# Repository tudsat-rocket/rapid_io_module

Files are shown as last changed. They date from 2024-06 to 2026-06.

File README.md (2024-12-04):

# I/O module

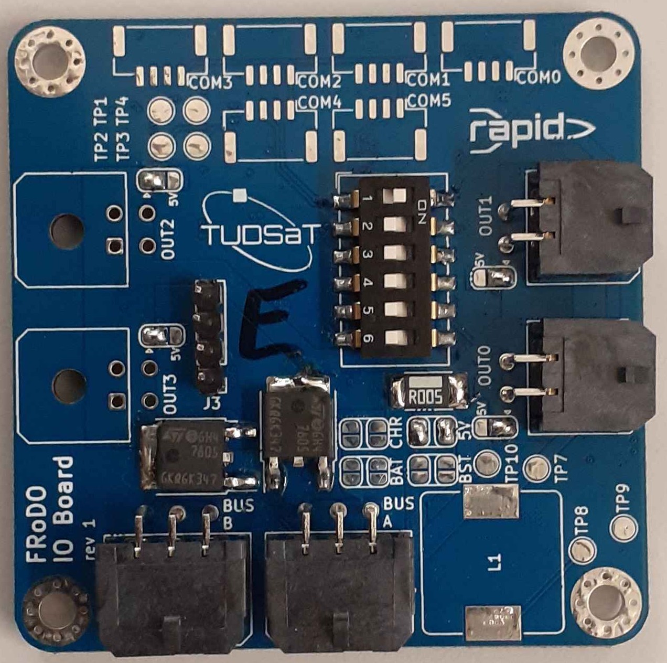
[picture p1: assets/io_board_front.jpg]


The I/O module is built as a general board for various sensor inputs and outputs. It is run by an STM32F103.

The module features 4 output connectors, with each being usable both as a servo output or 2 switchable outputs, powered by one of a variety of power sources. They also feature a variety of communication ports, allowing the connection to UART, I2C systems as well as the use of the STM32's ADC.

The outputs of the I/O module can be powered straight from the FC battery, a 5v line powered by a linear regulator, an external source like the charge bus or an auxiliary battery, or an onboard, programmable boost converter.

## Components

- STM32F103
- 4x output connector
- 2x switchable outputs
- see schematics for complete list

## Firmware

The firmware for the IO-board is written in rust, uses [embassy](https://github.com/embassy-rs/embassy) and can be found in the `frimware` folder. 

## Getting started

- clone the repository

- install STLink drivers
  
  - **Linux**: Install via package manager if possible, e.g. `pacman -S stlink`
  
  - **Windows**:
    
    - Download drivers from [ST's website](https://www.st.com/en/development-tools/stsw-link009.html) (requires account)
    - Extract .zip and run `dpinst_amd64.exe` for 64-bit systems, and `dpinst_x86.exe` on 32-bit systems.
    
    After installation, it *may* be necessary to unplug the STLink and plug it back in, or even reboot (or reload udev rules on Linux).

- install **Rustup**
  
  - A tool used to manage different Rust versions and targets (e.g. x86, ARM,
     etc.). Download and run installer: follow the instructions on [https://rustup.rs/](https://rustup.rs/) (Use rustup-init.exe for Windows, defaults are fine)

- **Rust**
  
  - Using `rustup`, we can download the target needed for the STM32 and some other tools we need.
    
    - `rustup target add thumbv7em-none-eabi` (Add ARM toolchain)
    
    - `cargo install probe-rs-tools --locked`
    
    - `cargo install flip-link` (Needed for cargo run)

- **Compiling & Flashing**
  
  - run `cargo run --release`

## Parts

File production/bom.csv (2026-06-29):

Designator | Footprint | Quantity | Value | LCSC Part #
C1 | 0402 | 1 | 4u7
C10, C7 | 0402 | 2 | 10n
C11, C12, C13 | 0805 | 3 | 10u | C440198
C14 | CP_Elec_6.3x4.5 | 1 | 220u | C5379968
C15, C16 | 0805 | 2 | 22u | C45783
C17 | 0805 | 1 | 10u | C15850
C18, C20, C30 | 0402 | 3 | 100n | C1525
C19 | 0603 | 1 | 470n | C1623
C2, C29, C3, C31, C32, C33, C34, C35, C38, C4, C41, C5, C6 | 0402 | 13 | 100n
C21, C22, C23, C24, C36, C37, C39, C40, C42, C43 | 0402 | 10 | 10n | C15195
C25, C26 | 0402 | 2 | 10p
C27 | 0402 | 1 | 10u | C15525
C28 | 0603 | 1 | 22u | C59461
C8, C9 | 0402 | 2 | 1u
D1, D7 | D_SMA | 2 | 700mV@5A | C5140024
D10, D13, D14, D9 | D_SOD-123FL | 4 | D | C64898
D11, D12, D15, D16, D2, D3, D4, D5, D6 | 0603 | 9 | red | C2286
D8 | D_SOD-123 | 1 | ~ | C8598
F1 | 1206 | 1 | 3A | C14165
F2, F3 | 1206 | 2 | 5A | C57525
FB1 | 0603 | 1 | 120R
J15 | USB_C_Receptacle_Palconn_UTC16-G | 1 | USB_C_Receptacle_USB2.0 | C709357
Q1, Q2, Q5, Q6 | SOIC-8_3.9x4.9mm_P1.27mm | 4 | AOSP21321 | C560863
Q10, Q11, Q12, Q9 | SOT-23 | 4 | AO3400A | C20917
R1 | 0402 | 1 | 17k4 | C2933077
R10, R18, R19, R9 | 0603 | 4 | 4k7 | C23162
R11, R38, R39, R7, R8 | 0402 | 5 | 22R | C25092
R12, R13, R15, R16, R20, R21, R23, R24 | 0402 | 8 | 100
R14, R17, R22, R25, R26, R27, R28, R29, R3, R30, R5, R69, R70, R71, R72, R73, R74 | 0402 | 17 | 1k | C11702
R2, R32, R33 | 1206 | 3 | 15m | C601098
R31, R6 | 0402 | 2 | 100k | C25741
R34, R35, R36, R37, R44 | 0402 | 5 | 5k1 | C25905
R4 | 0402 | 1 | 3k3 | C25890
R41, R42, R43 | 0402 | 3 | 15k | C25756
R45, R46, R47 | 0402 | 3 | 2k2 | C25879
R49, R50, R51, R52, R53, R54, R57, R58, R59, R60, R61, R62, R63, R64, R67, R68 | 0402 | 16 | 12k | C25752
R55, R56, R65, R66 | 0402 | 4 | 330 | C25104
SW1, SW2, SW3 | SW_SPST_TS-1088-xR020 | 3 | KMR721NGLFS | C720477
TH1 | 0603 | 1 | 10k
TP1, TP2, TP3, TP4, TP5 | TestPoint_Pad_D1.0mm | 5 | TestPoint
U2 | LQFP-64_10x10mm_P0.5mm | 1 | STM32F105RCTx
U3 | SOT-223-3_TabPin2 | 1 | AZ1117-3.3 | C92102
U4 | SOIC-8_5.3x5.3mm_P1.27mm | 1 | W25Q128JVP
U5, U6 | SOIC-8_3.9x4.9mm_P1.27mm | 2 | MCP2562-E-SN
U7, U8, U9 | SOT-23-6 | 3 | INA181A1 | C45351496
Y1 | Crystal_SMD_5032-4Pin_5.0x3.2mm | 1 | 8MHz 12pF | C2149245

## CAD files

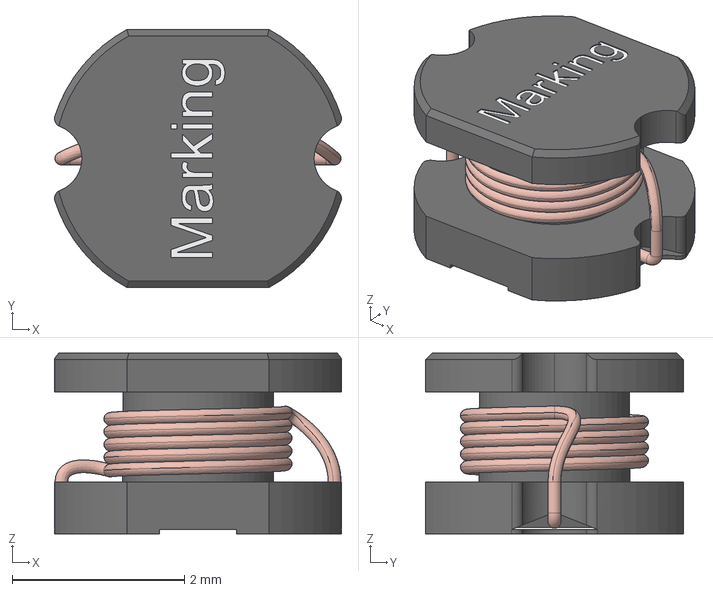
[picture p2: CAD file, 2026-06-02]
3dmodels/L_Wurth_WE-PD2-3521.step
3.34 x 3.00 x 2.10 mm

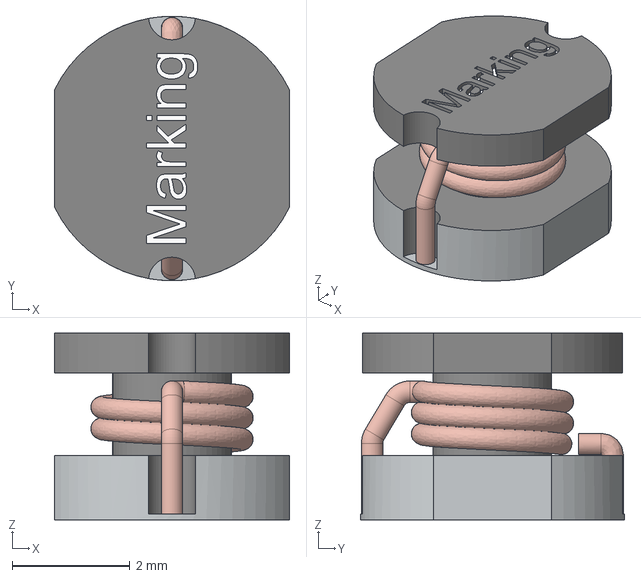
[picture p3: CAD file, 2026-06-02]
3dmodels/L_Wurth_WE-PD2-4532.step
4.00 x 4.50 x 3.18 mm

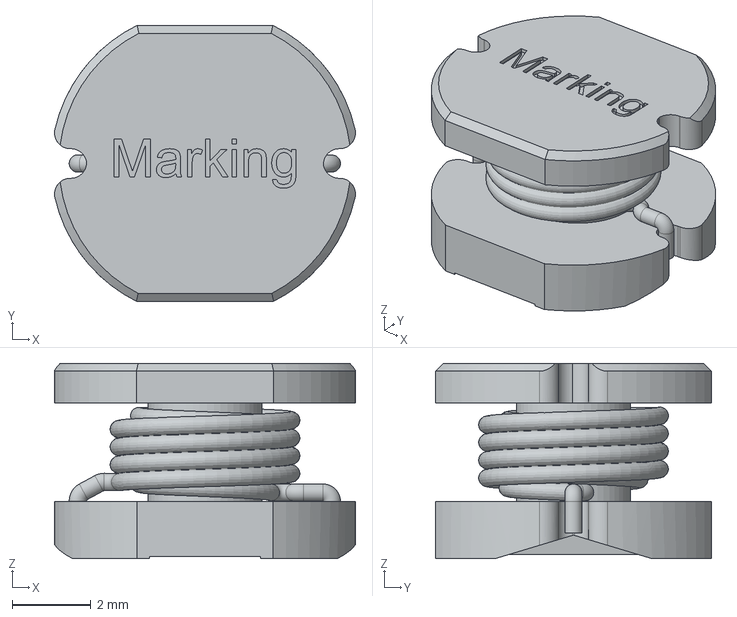
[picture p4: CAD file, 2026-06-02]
3dmodels/L_Wurth_WE-PD2-7850.step
7.63 x 7.00 x 4.95 mm

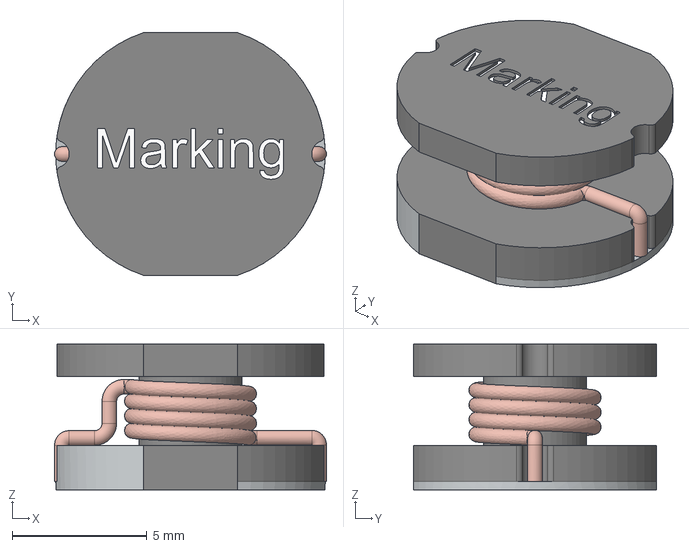
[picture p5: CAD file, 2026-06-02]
3dmodels/L_Wurth_WE-PD2-1054.step
10.1 x 9.00 x 5.40 mm

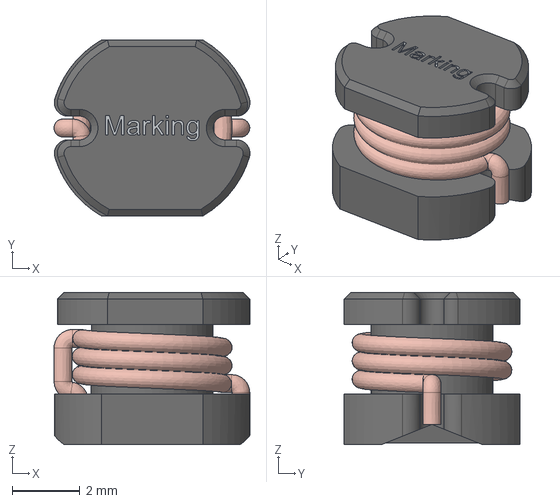
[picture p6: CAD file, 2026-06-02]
3dmodels/L_Wurth_WE-PD2-5848.step
5.79 x 5.20 x 4.50 mm

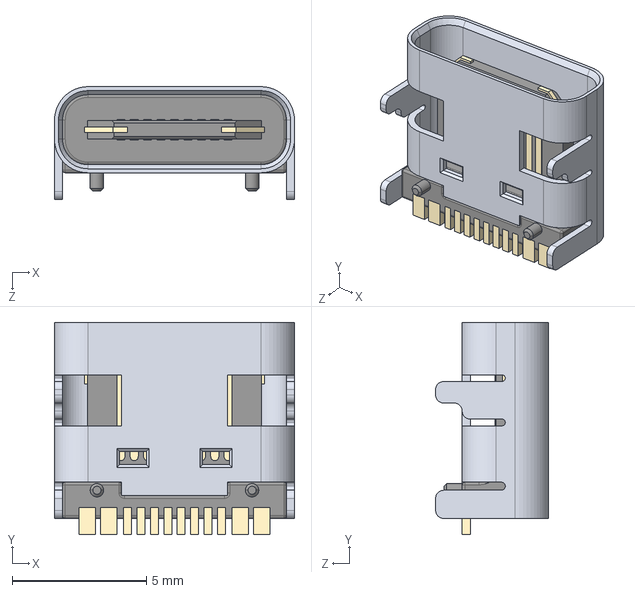
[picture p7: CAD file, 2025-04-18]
3dmodels/usb_c.step
8.94 x 7.90 x 4.20 mm

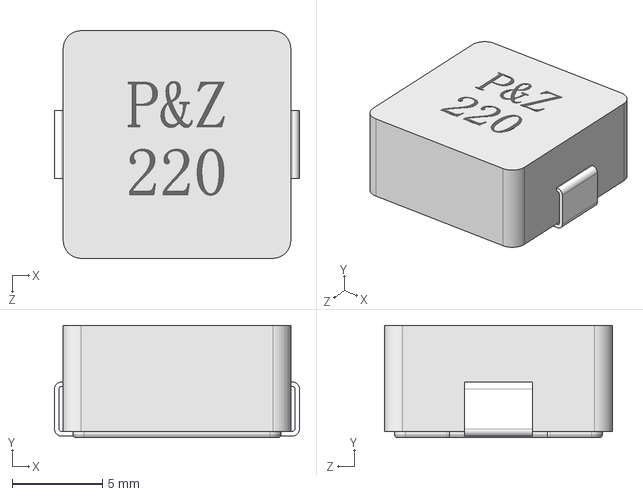
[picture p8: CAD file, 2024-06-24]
3dmodels/PSM1365 Series SMD Molding inductor.STEP
13.6 x 6.21 x 12.6 mm

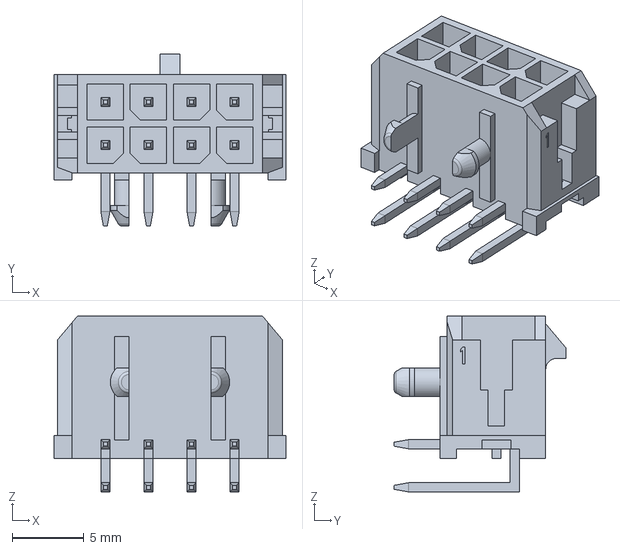
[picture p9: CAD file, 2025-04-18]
3dmodels/430450800.stp
16.1 x 11.9 x 12.2 mm

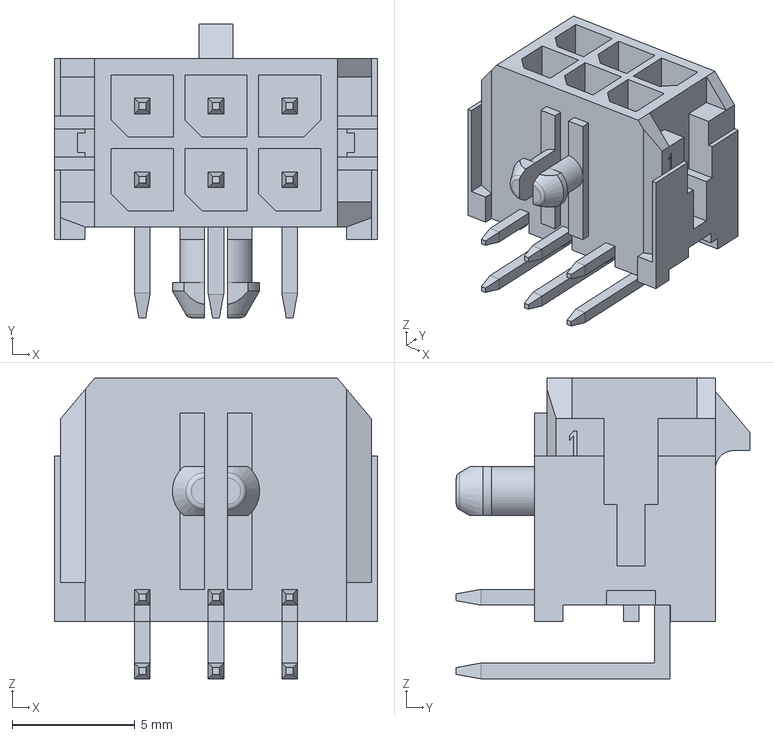
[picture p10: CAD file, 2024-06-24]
3dmodels/430450600.stp
13.2 x 11.9 x 12.2 mm

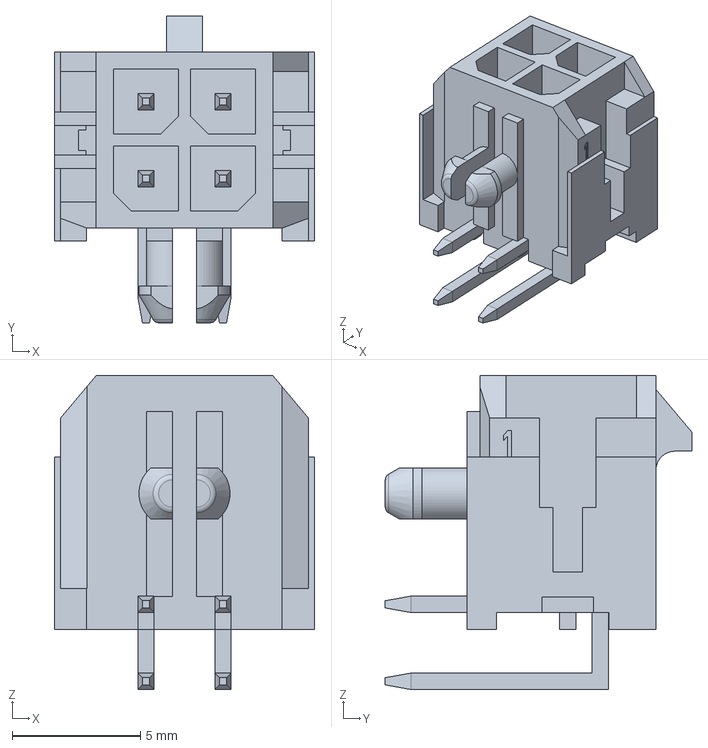
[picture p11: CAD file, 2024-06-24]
3dmodels/430450400.step
10.2 x 11.9 x 12.2 mm

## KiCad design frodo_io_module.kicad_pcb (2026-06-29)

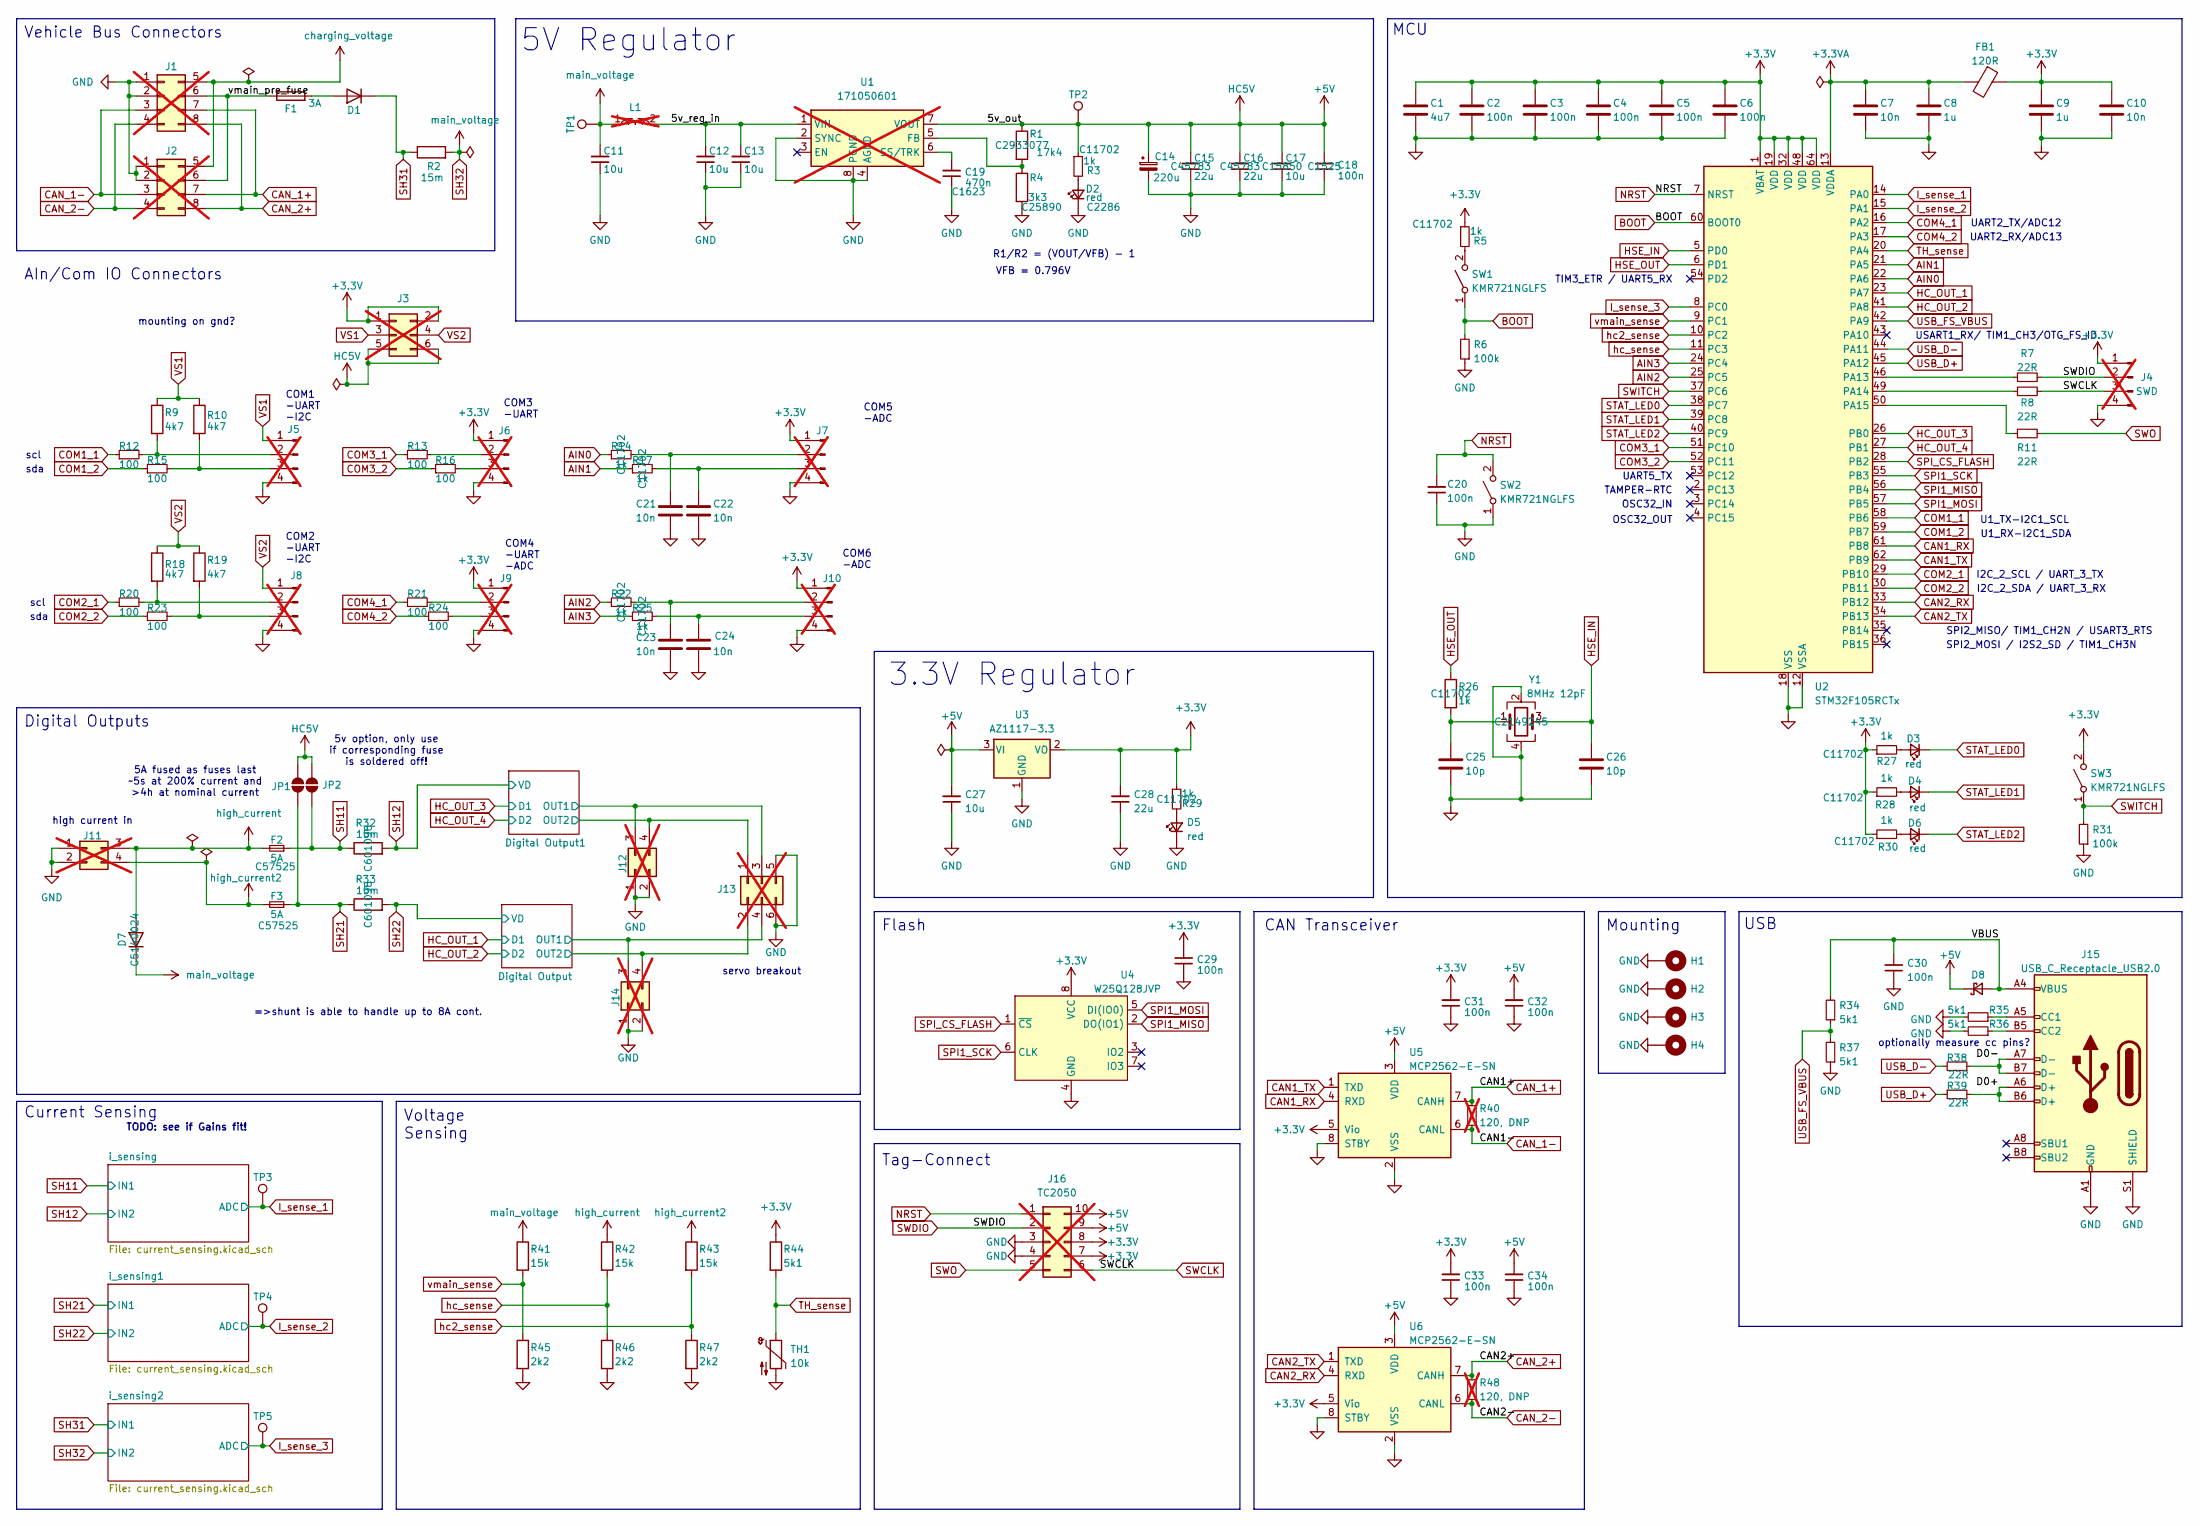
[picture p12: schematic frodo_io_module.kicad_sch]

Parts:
C1: 4u7; C_0402_1005Metric; LCSC# C23733
C2, C3, C4, C5, C6, C29, C31, C32, C33, C34: 100n; C_0402_1005Metric; LCSC# C1525
C7, C10: 10n; C_0402_1005Metric; LCSC# C15195
C8, C9: 1u; C_0402_1005Metric; LCSC# C52923
C11, C12, C13: 10u; C_0805_2012Metric; LCSC C440198
C14: 220u; CP_Elec_6.3x4.5; LCSC C5379968
C15, C16: 22u; C_0805_2012Metric; LCSC C45783
C17: 10u; C_0805_2012Metric; LCSC C15850
C18: 100n; C_0402_1005Metric; LCSC C1525
C19: 470n; C_0603_1608Metric; LCSC C1623
C20, C30: 100n; C_0402_1005Metric; Part# CL10B104KB8NNNC; LCSC C1525
C21, C22, C23, C24: 10n; C_0402_1005Metric; LCSC C15195
C25, C26: 10p; C_0402_1005Metric; LCSC# C32949
C27: 10u; C_0402_1005Metric; Part# CL31B106KAHNNNE; LCSC C15525
C28: 22u; C_0603_1608Metric; Part# GRM155R60J226ME11D; LCSC C59461
D1, D7: 700mV@5A; D_SMA; LCSC C5140024
D2: red; LED_0603_1608Metric; Part# XL-1608SURC-06; LCSC C2286
D3, D4, D5, D6: red; LED_0603_1608Metric; LCSC C2286
D8: D_SOD-123; Part# PMEG3020EH,115; LCSC C8598
F1: 3A; Fuse_1206_3216Metric_Pad1.42x1.75mm_HandSolder; LCSC C14165
F2, F3: 5A; Fuse_1206_3216Metric_Pad1.42x1.75mm_HandSolder; Part# 0466005.NRHF; LCSC C57525
FB1: 120R; L_0603_1608Metric; Part# BLM18PG121SN1D; LCSC# C14709
H1, H2, H3, H4: MountingHole_Pad; MountingHole_3.2mm_M3_Pad_Via; DigiKey# N/A
J1, J2: Conn_02x04_Top_Bottom; Molex_Micro-Fit_3.0_43045-0800_2x04_P3.00mm_Horizontal; LCSC x; not fitted
J3: Conn_02x03_Odd_Even; PinHeader_2x03_P1.27mm_Vertical_SMD; not fitted
J4: SWD; PinHeader_1x04_P2.54mm_Vertical; not fitted
J5, J6, J8, J9: JST-GH 4Pin; JST_GH_SM04B-GHS-TB_1x04-1MP_P1.25mm_Horizontal; not fitted
J7, J10: JST-GH 4Pin; JST_GH_BM04B-GHS-TBT_1x04-1MP_P1.25mm_Vertical; not fitted
J11: Molex_Micro-Fit_3.0_43045-0400_2x02_P3.00mm_Horizontal; LCSC# x; not fitted
J12, J14: Molex_Micro-Fit_3.0_43045-0400_2x02_P3.00mm_Horizontal; not fitted
J13: Conn_02x03_Odd_Even; PinHeader_2x03_P2.54mm_Vertical; not fitted
J15: USB_C_Receptacle_USB2.0; USB_C_Receptacle_Palconn_UTC16-G; Part# KH-TYPE-C-16P; LCSC C709357
J16: TC2050; Tag-Connect_TC2050-IDC-FP_2x05_P1.27mm_Vertical; not fitted
JP1, JP2: SolderJumper_2_Open; SolderJumper-2_P1.3mm_Open_RoundedPad1.0x1.5mm
L1: 2.2uH; L_Wurth_WE-PD2-5848; Part Number 744774022; not fitted
R1: 17k4; R_0402_1005Metric; LCSC C2933077
R2, R32, R33: 15m; R_1206_3216Metric_Pad1.30x1.75mm_HandSolder; Part# HoLR1206-1W-15mR-1%-75ppm; LCSC C601098
R3, R5, R14, R17, R22, R25, R26, R27, R28, R29, R30: 1k; R_0402_1005Metric; LCSC C11702
R4: 3k3; R_0402_1005Metric; LCSC C25890
R6, R31: 100k; R_0402_1005Metric; Part# RC0603FR-0710KL; LCSC C25741
R7, R8, R11: 22R; R_0402_1005Metric; Part# RC0603FR-0710KL; LCSC C25092
R9, R10, R18, R19: 4k7; R_0603_1608Metric_Pad0.98x0.95mm_HandSolder; LCSC C23162
R12, R13, R15, R16, R20, R21, R23, R24: 100; R_0402_1005Metric; Part# RC0402FR-07100RL; LCSC# C106232
R34, R37: 5k1; R_0402_1005Metric; Part# RC0603FR-0710KL; LCSC C25905
R35, R36: 5k1; R_0402_1005Metric; Part# RC0603FR-075K1L; LCSC C25905
R38, R39: 22R; R_0402_1005Metric; Part# RC0603FR-0722RL; LCSC C25092
R40, R48: 120, DNP; R_0603_1608Metric_Pad0.98x0.95mm_HandSolder; LCSC# x; not fitted
R41, R42, R43: 15k; R_0402_1005Metric; LCSC C25756
R44: 5k1; R_0402_1005Metric; LCSC C25905
R45, R46, R47: 2k2; R_0402_1005Metric; LCSC C25879
SW1, SW2, SW3: KMR721NGLFS; SW_SPST_TS-1088-xR020; Part# KMR721NGLFS; LCSC C720477
TH1: 10k; R_0603_1608Metric_Pad0.98x0.95mm_HandSolder; Part# NCP18XH103F03RB; LCSC# C13564
TP1, TP2, TP3, TP4, TP5: TestPoint; TestPoint_Pad_D1.0mm
U1: 171050601; TO-263-7_TabPin8; not fitted
U2: STM32F105RCTx; LQFP-64_10x10mm_P0.5mm; LCSC C8345
U3: AZ1117-3.3; SOT-223-3_TabPin2; LCSC C92102
U4: W25Q128JVP; SOIC-8_5.3x5.3mm_P1.27mm; Part# W25Q128JVSIQ; LCSC# C97521
U5, U6: MCP2562-E-SN; SOIC-8_3.9x4.9mm_P1.27mm; Part# MCP2562T-E/SN; LCSC# C191417
Y1: 8MHz 12pF; Crystal_SMD_5032-4Pin_5.0x3.2mm; Part# 5TJ480000NYLBC; LCSC C2149245

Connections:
+3.3V: C1.1, C2.1, C3.1, C4.1, C5.1, C6.1, C9.1, C10.1, C28.2, C29.2, C31.2, C33.2, FB1.1, J3.1, J3.2, J4.1, J6.1, J7.1, J9.1, J10.1, J16.7, J16.8, R5.1, R27.1, R28.1, R29.1, R30.1, R44.1, SW3.2 (B), U2.1 (VBAT), U2.19 (VDD), U2.32 (VDD), U2.48 (VDD), U2.64 (VDD), U3.2 (VO), U4.8 (VCC), U5.5 (Vio), U6.5 (Vio); also elsewhere on the board
+3.3VA: C7.1, C8.1, FB1.2, U2.13 (VDDA)
+5V: C14.1, C15.2, C16.2, C17.2, C18.2, C27.2, C32.2, C34.2, D8.1 (K), J3.5, J3.6, J16.9, J16.10, JP1.2 (B), JP2.2 (B), R1.1, R3.1, TP2.1 (1_1), U1.7 (VOUT), U3.3 (VI), U5.3 (VDD), U6.3 (VDD)
/5v_reg_in: C12.2, C13.2, L1.2, U1.1 (VIN)
/D0+: J15.A6 (D+), J15.B6 (D+), R39.2
/D0-: J15.A7 (D-), J15.B7 (D-), R38.1
/Digital Output1/OUT1: J12.3, J13.3; also elsewhere on the board
/Digital Output1/OUT2: J12.4, J13.1; also elsewhere on the board
/Digital Output/OUT1: J13.4, J14.3; also elsewhere on the board
/Digital Output/OUT2: J13.2, J14.4; also elsewhere on the board
/VBUS: C30.2, D8.2 (A), J15.A4 (VBUS), J15.A9 (VBUS), J15.B4 (VBUS), J15.B9 (VBUS), R34.2
/vmain_pre_fuse: F1.1, J1.6, J2.6
AIN0: R14.1, U2.22 (PA6)
AIN1: R17.1, U2.21 (PA5)
AIN2: R22.1, U2.25 (PC5)
AIN3: R25.1, U2.24 (PC4)
BOOT: R6.2, SW1.1 (A), U2.60 (BOOT0)
CAN1_RX: U2.61 (PB8), U5.4 (RXD)
CAN1_TX: U2.62 (PB9), U5.1 (TXD)
CAN2_RX: U2.33 (PB12), U6.4 (RXD)
CAN2_TX: U2.34 (PB13), U6.1 (TXD)
CAN_1+: J1.7, J2.7, R40.1, U5.7 (CANH)
CAN_1-: J1.3, J2.3, R40.2, U5.6 (CANL)
CAN_2+: J1.8, J2.8, R48.1, U6.7 (CANH)
CAN_2-: J1.4, J2.4, R48.2, U6.6 (CANL)
COM1_1: R12.1, U2.58 (PB6)
COM1_2: R15.1, U2.59 (PB7)
COM2_1: R20.1, U2.29 (PB10)
COM2_2: R23.1, U2.30 (PB11)
COM3_1: R13.1, U2.51 (PC10)
COM3_2: R16.1, U2.52 (PC11)
COM4_1: R21.1, U2.16 (PA2)
COM4_2: R24.1, U2.17 (PA3)
GND: C1.2, C2.2, C3.2, C4.2, C5.2, C6.2, C7.2, C8.2, C9.2, C10.2, C11.1, C12.1, C13.1, C14.2, C15.1, C16.1, C17.1, C18.1, C19.1, C20.1, C21.2, C22.2, C23.2, C24.2, C25.2, C26.2, C27.1, C28.1, C29.1, C30.1, C31.1, C32.1, C33.1, C34.1, D2.1 (K), D5.1 (K), H1.1 (1_1), H2.1 (1_1), H3.1 (1_1), H4.1 (1_1), J1.1, J1.2, J2.1, J2.2, J4.4, J5.4, J6.4, J7.4, J8.4, J9.4, J10.4, J11.1, J11.2, J12.1, J12.2, J13.5, J13.6, J14.1, J14.2, J15.A1 (GND), J15.A12 (GND), J15.B1 (GND), J15.B12 (GND), J15.S1 (SHIELD), J16.3, J16.4, R4.2, R6.1, R31.1, R35.2, R36.2, R37.1, R45.2, R46.2, R47.2, SW2.1 (A), TH1.2, U1.2 (SYNC), U1.4 (AGND), U1.8 (PGND), U2.12 (VSSA), U2.18 (VSS), U2.31 (VSS), U2.47 (VSS), U2.63 (VSS), U3.1 (GND), U4.4 (GND), U5.2 (VSS), U5.8 (STBY), U6.2 (VSS), U6.8 (STBY), Y1.2, Y1.4; also elsewhere on the board
HC_OUT_1: U2.23 (PA7); also elsewhere on the board
HC_OUT_2: U2.41 (PA8); also elsewhere on the board
HC_OUT_3: U2.26 (PB0); also elsewhere on the board
HC_OUT_4: U2.27 (PB1); also elsewhere on the board
HSE_IN: C26.1, U2.5 (PD0), Y1.3
HSE_OUT: R26.1, U2.6 (PD1)
I_sense_1: TP3.1 (1_1), U2.14 (PA0); also elsewhere on the board
I_sense_2: TP4.1 (1_1), U2.15 (PA1); also elsewhere on the board
I_sense_3: TP5.1 (1_1), U2.8 (PC0); also elsewhere on the board
NRST: C20.2, J16.1, SW2.2 (B), U2.7 (NRST)
unnamed: C25.1, R26.2, Y1.1
unnamed: D1.2 (A), F1.2
unnamed: D2.2 (A), R3.2
unnamed: D3.2 (A), R27.2
unnamed: D4.2 (A), R28.2
unnamed: D5.2 (A), R29.2
unnamed: D6.2 (A), R30.2
unnamed: J5.2, R9.2, R12.2
unnamed: J5.3, R10.2, R15.2
unnamed: J6.2, R13.2
unnamed: J6.3, R16.2
unnamed: C21.1, J7.2, R14.2
unnamed: C22.1, J7.3, R17.2
unnamed: J8.2, R18.2, R20.2
unnamed: J8.3, R19.2, R23.2
unnamed: J9.2, R21.2
unnamed: J9.3, R24.2
unnamed: C23.1, J10.2, R22.2
unnamed: C24.1, J10.3, R25.2
unnamed: J15.A5 (CC1), R35.1
unnamed: J15.B5 (CC2), R36.1
unnamed: R5.2, SW1.2 (B)
unnamed: R1.2, R4.1, U1.5 (FB)
unnamed: C19.2, U1.6 (SS/TRK)
unnamed: R7.1, U2.46 (PA13)
unnamed: R8.1, U2.49 (PA14)
unnamed: R11.1, U2.50 (PA15)
SH11: F2.1, JP2.1 (A), R32.1; also elsewhere on the board
SH12: R32.2; also elsewhere on the board
SH21: F3.1, JP1.1 (A), R33.1; also elsewhere on the board
SH22: R33.2; also elsewhere on the board
SH31: D1.1 (K), R2.1; also elsewhere on the board
SH32: C11.2, D7.1 (K), L1.1, R2.2, R41.1, TP1.1 (1_1); also elsewhere on the board
SPI1_MISO: U2.56 (PB4), U4.2 (DO(IO1))
SPI1_MOSI: U2.57 (PB5), U4.5 (DI(IO0))
SPI1_SCK: U2.55 (PB3), U4.6 (CLK)
SPI_CS_FLASH: U2.28 (PB2), U4.1 (~CS)
STAT_LED0: D3.1 (K), U2.38 (PC7)
STAT_LED1: D4.1 (K), U2.39 (PC8)
STAT_LED2: D6.1 (K), U2.40 (PC9)
SWCLK: J4.3, J16.6, R8.2
SWDIO: J4.2, J16.2, R7.2
SWITCH: R31.2, SW3.1 (A), U2.37 (PC6)
SWO: J16.5, R11.2
TH_sense: R44.2, TH1.1, U2.20 (PA4)
USB_D+: R39.1, U2.45 (PA12)
USB_D-: R38.2, U2.44 (PA11)
USB_FS_VBUS: R34.1, R37.2, U2.42 (PA9)
VS1: J3.3, J5.1, R9.1, R10.1
VS2: J3.4, J8.1, R18.1, R19.1
charging_voltage: J1.5, J2.5
hc2_sense: R43.2, R47.1, U2.10 (PC2)
hc_sense: R42.2, R46.1, U2.11 (PC3)
high_current: D7.2 (A), F2.2, J11.3, R42.1
high_current2: F3.2, J11.4, R43.1
vmain_sense: R41.2, R45.1, U2.9 (PC1)

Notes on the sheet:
scl
Vehicle Bus Connectors
servo breakout
3.3V Regulator
TIM3_ETR / UART5_RX
U1_RX-I2C1_SDA
SPI2_MISO/ TIM1_CH2N / USART3_RTS
OSC32_IN
I2C_2_SCL / UART_3_TX
VFB = 0.796V
USART1_RX/ TIM1_CH3/OTG_FS_ID
COM4 -UART -ADC
Mounting
OSC32_OUT
COM2 -UART -I2C
COM6 -ADC
5v option, only use if corresponding fuse is soldered off!
USB
5A fused as fuses last ~5s at 200% current and >4h at nominal current
Voltage Sensing
CAN Transceiver
TODO: see if Gains fit!
=>shunt is able to handle up to 8A cont.
U1_TX-I2C1_SCL
optionally measure cc pins?
COM3 -UART
AIn/Com IO Connectors
UART2_RX/ADC13
SPI2_MOSI / I2S2_SD / TIM1_CH3N
sda
5V Regulator
UART5_TX
Digital Outputs
R1/R2 = (VOUT/VFB) - 1
MCU
TAMPER-RTC
UART2_TX/ADC12
Current Sensing
high current in
mounting on gnd?

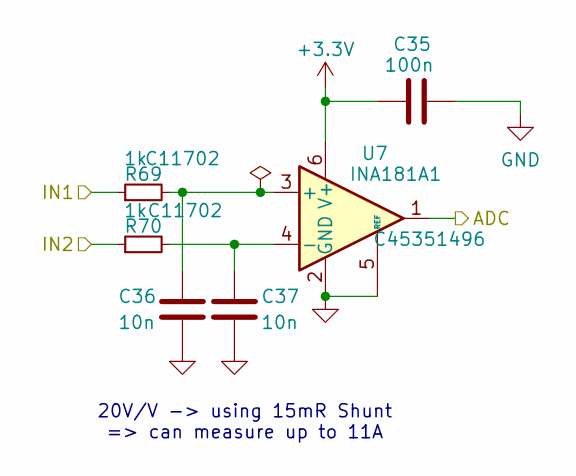
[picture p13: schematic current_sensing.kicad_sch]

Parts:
C35: 100n; C_0402_1005Metric; LCSC# C1525
C36, C37: 10n; C_0402_1005Metric; LCSC C15195
R69, R70: 1k; R_0402_1005Metric; LCSC C11702
U7: INA181A1; SOT-23-6; LCSC C45351496

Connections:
+3.3V: C35.1, U7.6 (V+); also elsewhere on the board
GND: C35.2, C36.2, C37.2, U7.2 (GND), U7.5 (REF); also elsewhere on the board
I_sense_1: U7.1; also elsewhere on the board
unnamed: C36.1, R69.2, U7.3 (+)
unnamed: C37.1, R70.2, U7.4 (-)
SH11: R69.1; also elsewhere on the board
SH12: R70.1; also elsewhere on the board

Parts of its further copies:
C38, C41: 100n; C_0402_1005Metric; LCSC# C1525
C39, C40, C42, C43: 10n; C_0402_1005Metric; LCSC C15195
R71, R72, R73, R74: 1k; R_0402_1005Metric; LCSC C11702
U8, U9: INA181A1; SOT-23-6; LCSC C45351496

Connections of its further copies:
+3.3V: C38.1, C41.1, U8.6 (V+), U9.6 (V+); also elsewhere on the board
GND: C38.2, C39.2, C40.2, C41.2, C42.2, C43.2, U8.2 (GND), U8.5 (REF), U9.2 (GND), U9.5 (REF); also elsewhere on the board
I_sense_2: U8.1; also elsewhere on the board
I_sense_3: U9.1; also elsewhere on the board
unnamed: C39.1, R71.2, U8.3 (+)
unnamed: C40.1, R72.2, U8.4 (-)
unnamed: C42.1, R73.2, U9.3 (+)
unnamed: C43.1, R74.2, U9.4 (-)
SH21: R71.1; also elsewhere on the board
SH22: R72.1; also elsewhere on the board
SH31: R73.1; also elsewhere on the board
SH32: R74.1; also elsewhere on the board

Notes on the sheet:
20V/V -> using 15mR Shunt => can measure up to 11A

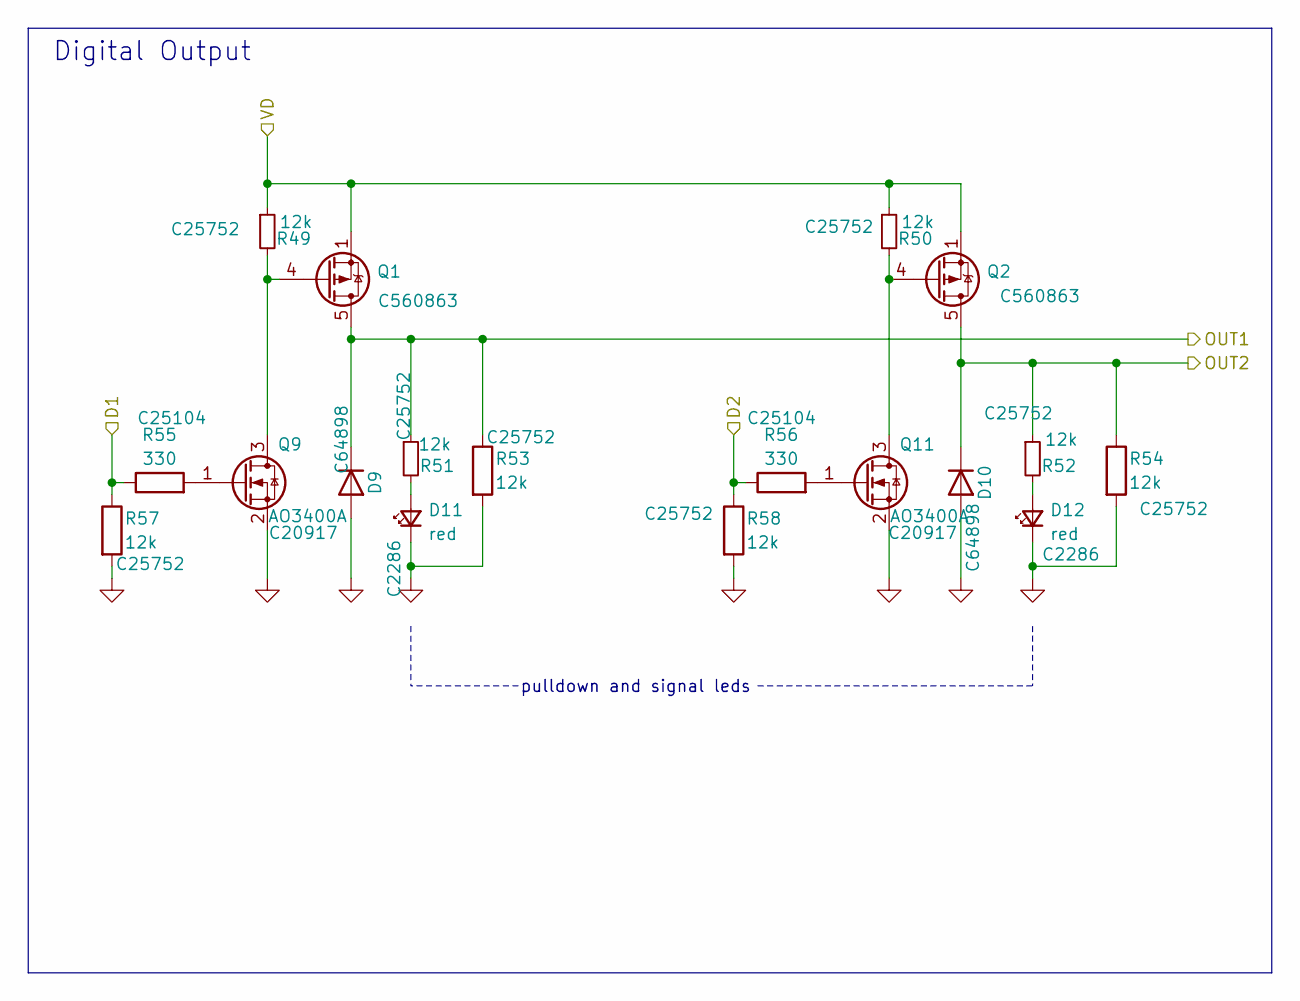
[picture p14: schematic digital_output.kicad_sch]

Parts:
D9, D10: D; D_SOD-123FL; LCSC C64898
D11, D12: red; LED_0603_1608Metric; LCSC C2286
Q1, Q2: AOSP21321; SOIC-8_3.9x4.9mm_P1.27mm; Part# AOSP21321; LCSC C560863
Q9, Q11: AO3400A; SOT-23; LCSC C20917
R49, R50, R51, R52, R53, R54, R57, R58: 12k; R_0402_1005Metric; LCSC C25752
R55, R56: 330; R_0402_1005Metric; LCSC C25104

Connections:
/Digital Output/OUT1: D9.1 (K), Q1.5 (D), Q1.6 (D), Q1.7 (D), Q1.8 (D), R51.1, R53.1; also elsewhere on the board
/Digital Output/OUT2: D10.1 (K), Q2.5 (D), Q2.6 (D), Q2.7 (D), Q2.8 (D), R52.1, R54.1; also elsewhere on the board
GND: D9.2 (A), D10.2 (A), D11.1 (K), D12.1 (K), Q9.2 (S), Q11.2 (S), R53.2, R54.2, R57.2, R58.2; also elsewhere on the board
HC_OUT_1: R55.1, R57.1; also elsewhere on the board
HC_OUT_2: R56.1, R58.1; also elsewhere on the board
unnamed: D11.2 (A), R51.2
unnamed: D12.2 (A), R52.2
unnamed: Q1.4 (G), Q9.3 (D), R49.2
unnamed: Q9.1 (G), R55.2
unnamed: Q2.4 (G), Q11.3 (D), R50.2
unnamed: Q11.1 (G), R56.2
SH22: Q1.1 (S), Q1.2 (S), Q1.3 (S), Q2.1 (S), Q2.2 (S), Q2.3 (S), R49.1, R50.1; also elsewhere on the board

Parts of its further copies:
D13, D14: D; D_SOD-123FL; LCSC C64898
D15, D16: red; LED_0603_1608Metric; LCSC C2286
Q5, Q6: AOSP21321; SOIC-8_3.9x4.9mm_P1.27mm; Part# AOSP21321; LCSC C560863
Q10, Q12: AO3400A; SOT-23; LCSC C20917
R59, R60, R61, R62, R63, R64, R67, R68: 12k; R_0402_1005Metric; LCSC C25752
R65, R66: 330; R_0402_1005Metric; LCSC C25104

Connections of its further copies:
/Digital Output1/OUT1: D13.1 (K), Q5.5 (D), Q5.6 (D), Q5.7 (D), Q5.8 (D), R61.1, R63.1; also elsewhere on the board
/Digital Output1/OUT2: D14.1 (K), Q6.5 (D), Q6.6 (D), Q6.7 (D), Q6.8 (D), R62.1, R64.1; also elsewhere on the board
GND: D13.2 (A), D14.2 (A), D15.1 (K), D16.1 (K), Q10.2 (S), Q12.2 (S), R63.2, R64.2, R67.2, R68.2; also elsewhere on the board
HC_OUT_3: R65.1, R67.1; also elsewhere on the board
HC_OUT_4: R66.1, R68.1; also elsewhere on the board
unnamed: D15.2 (A), R61.2
unnamed: D16.2 (A), R62.2
unnamed: Q5.4 (G), Q10.3 (D), R59.2
unnamed: Q10.1 (G), R65.2
unnamed: Q6.4 (G), Q12.3 (D), R60.2
unnamed: Q12.1 (G), R66.2
SH12: Q5.1 (S), Q5.2 (S), Q5.3 (S), Q6.1 (S), Q6.2 (S), Q6.3 (S), R59.1, R60.1; also elsewhere on the board

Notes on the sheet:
pulldown and signal leds
Digital Output

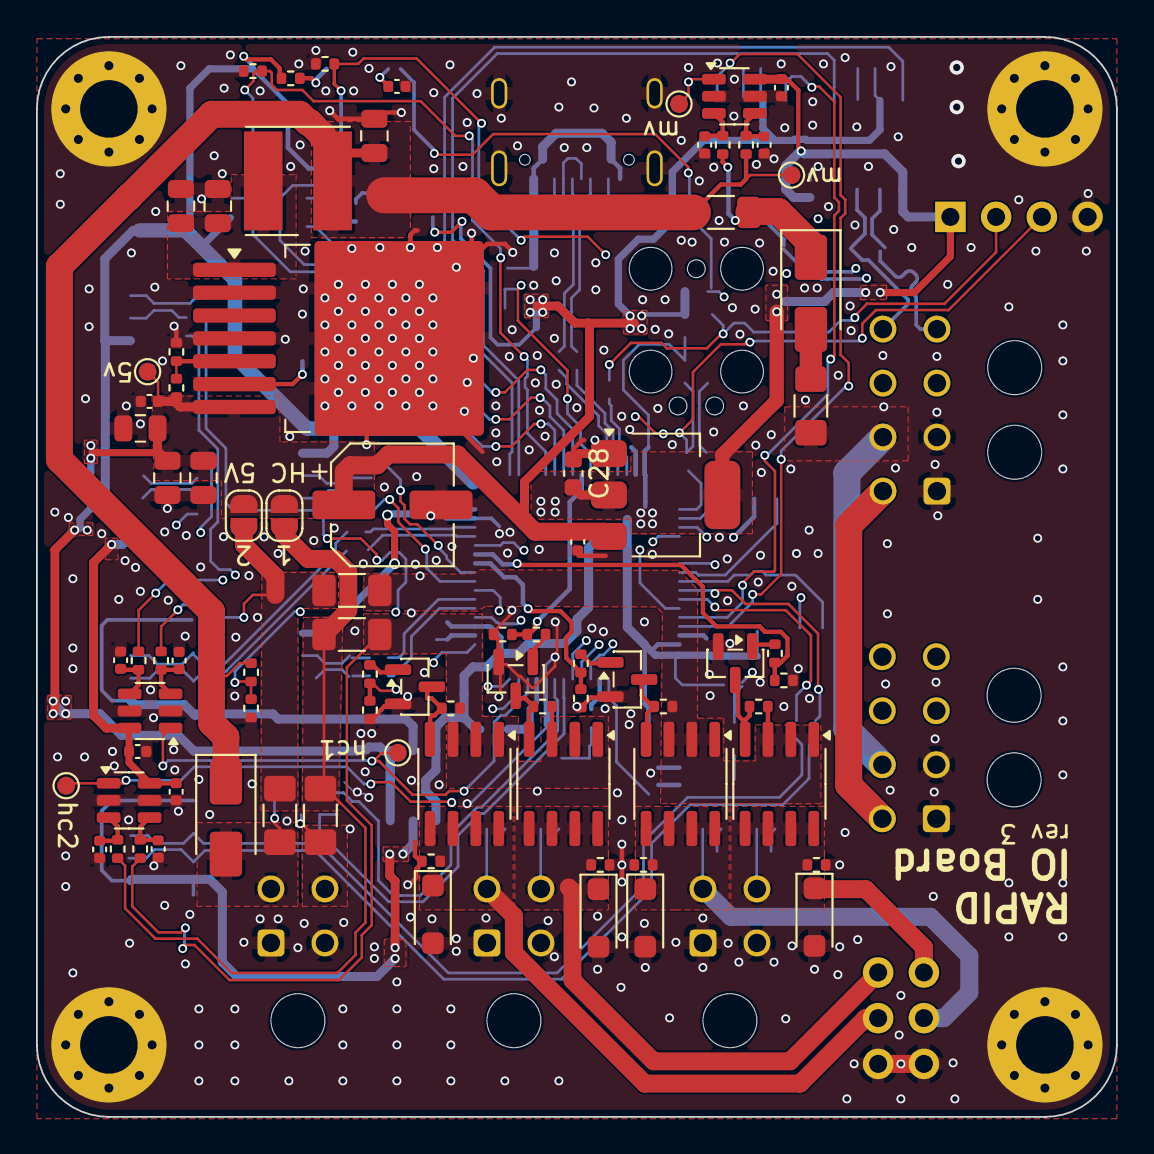
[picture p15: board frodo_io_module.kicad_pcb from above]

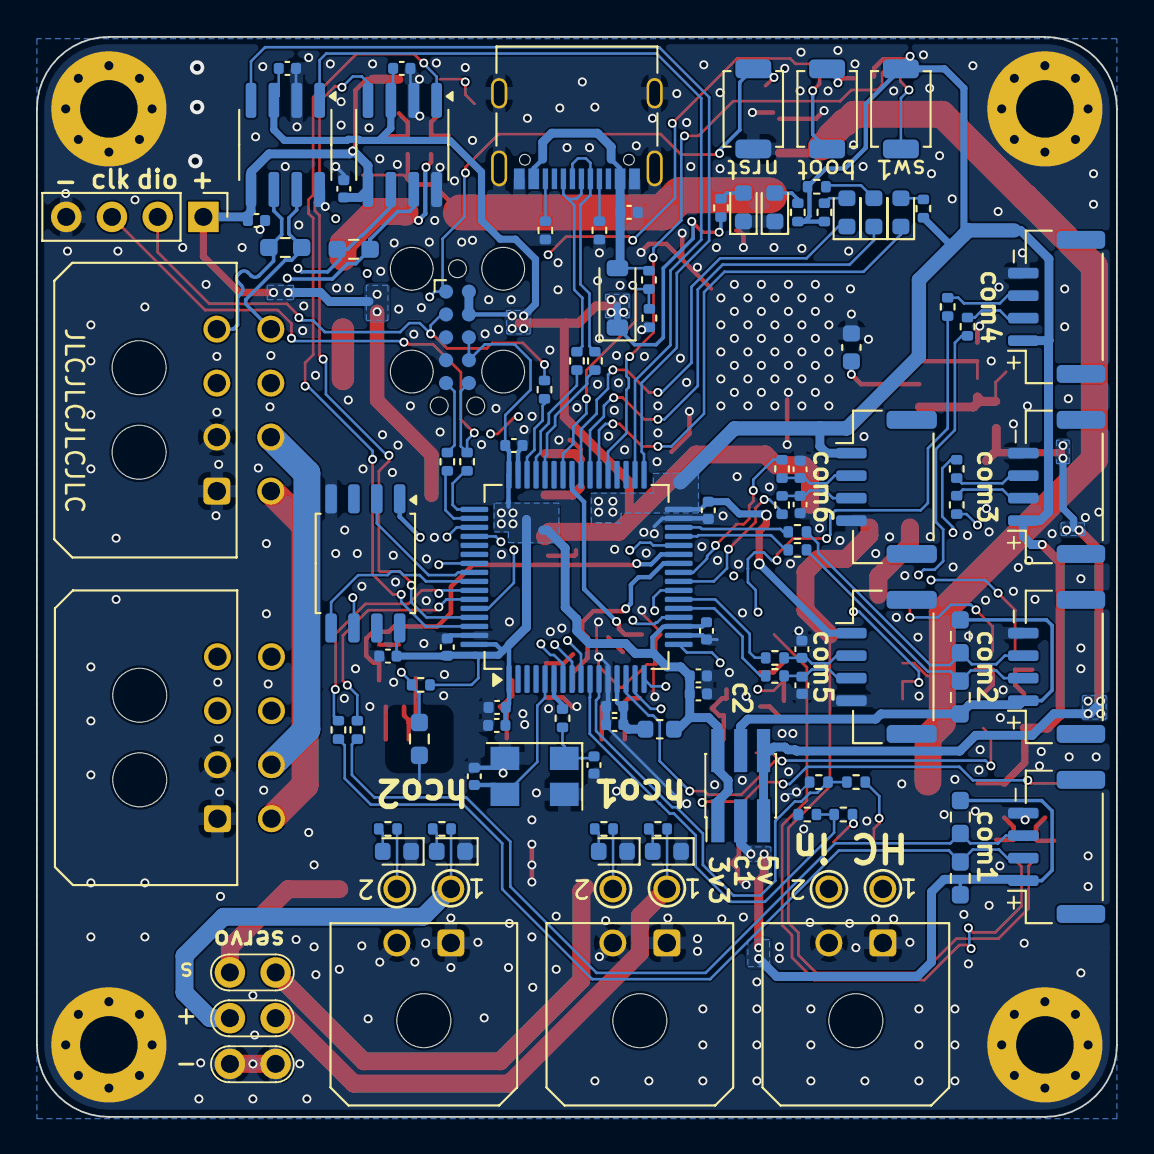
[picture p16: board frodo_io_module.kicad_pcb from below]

Board: 4 copper layers, 60.0 x 60.0 mm, 187 parts (101 on the bottom side), 118 nets.

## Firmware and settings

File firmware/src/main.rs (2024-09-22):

#![no_std]
#![no_main]

use embassy_executor::{InterruptExecutor, Spawner};
use embassy_stm32::adc::Adc;
use embassy_stm32::Config;
use embassy_stm32::gpio::{Input, Level, Output, Pull, Speed};
use embassy_stm32::i2c::I2c;
use embassy_stm32::interrupt::{Priority, InterruptExt};
use embassy_stm32::interrupt;
use embassy_stm32::peripherals::*;
use embassy_stm32::time::Hertz;
use embassy_stm32::usart::Uart;
use embassy_stm32::wdg::IndependentWatchdog;
use embassy_sync::blocking_mutex::raw::CriticalSectionRawMutex;
use embassy_sync::pubsub::{PubSubChannel, Publisher, Subscriber};
use embassy_time::{Delay, Duration, Ticker, Timer};
use shared_types::IoBoardRole;
use static_cell::StaticCell;

use {defmt_rtt as _, panic_probe as _};

mod boost;
mod can;
mod roles;

use boost::*;
use can::*;
use roles::*;
use roles::common::*;

type OutputStateChannel = PubSubChannel::<CriticalSectionRawMutex, ([bool; 8], bool), 1, 3, 2>;
type OutputStateSubscriber = Subscriber::<'static, CriticalSectionRawMutex, ([bool; 8], bool), 1, 3, 2>;
type OutputStatePublisher = Publisher::<'static, CriticalSectionRawMutex, ([bool; 8], bool), 1, 3, 2>;
static OUTPUT_STATE: StaticCell<OutputStateChannel> = StaticCell::new();

// TODO
#[global_allocator]
static ALLOCATOR: alloc_cortex_m::CortexMHeap = alloc_cortex_m::CortexMHeap::empty();

static EXECUTOR_HIGH: InterruptExecutor = InterruptExecutor::new();

embassy_stm32::bind_interrupts!(struct Irqs {
    CAN1_RX1 => embassy_stm32::can::Rx1InterruptHandler<CAN>;
    CAN1_SCE => embassy_stm32::can::SceInterruptHandler<CAN>;
    USB_LP_CAN1_RX0 => embassy_stm32::can::Rx0InterruptHandler<CAN>;
    USB_HP_CAN1_TX => embassy_stm32::can::TxInterruptHandler<CAN>;

    I2C1_EV => embassy_stm32::i2c::EventInterruptHandler<I2C1>;
    I2C1_ER => embassy_stm32::i2c::ErrorInterruptHandler<I2C1>;

    I2C2_EV => embassy_stm32::i2c::EventInterruptHandler<I2C2>;
    I2C2_ER => embassy_stm32::i2c::ErrorInterruptHandler<I2C2>;

    USART3 => embassy_stm32::usart::InterruptHandler<USART3>;
});

#[allow(dead_code)]
enum InputMode {
    Disabled,
    Uart(embassy_stm32::usart::Config),
    I2c(Hertz, embassy_stm32::i2c::Config),
    Adc,
    Gpio(Pull),
}

#[allow(dead_code)]
enum DriveVoltage {
    Battery,
    ChargeBus,
    BoostConverter,
    Regulator5V,
}

// == J7
#[allow(dead_code)]
enum Input0 {
    Disabled,
    //Uart(), // TODO: missing embassy support for asynchronous-only?
}

// == J6
#[allow(dead_code)]
enum Input1 {
    Disabled,
    Uart(Uart<'static, USART3, DMA1_CH2, DMA1_CH3>),
    I2c(I2c<'static, I2C2, DMA1_CH4, DMA1_CH5>),
}

// == J5
#[allow(dead_code)]
enum Input2 {
    Disabled,
    Uart, // TODO
    Adc, // TODO
}

// == J4
#[allow(dead_code)]
enum Input3 {
    Disabled,
    Uart, // TODO
    I2c(I2c<'static, I2C1, DMA1_CH6, DMA1_CH7>),
    Gpio(Input<'static, PB6>, Input<'static, PB7>),
}

// == J12
#[allow(dead_code)]
enum Input4 {
    Disabled,
    Adc, // TODO
}

// == J13
#[allow(dead_code)]
enum Input5 {
    Disabled,
    Adc, // TODO
}

/// Abstraction for the inputs and outputs. These are the same for all roles.
#[allow(dead_code)]
struct BoardIo {
    pub input0: Input0,
    pub input1: Input1,
    pub input2: Input2,
    pub input3: Input3,
    pub input4: Input4,
    pub input5: Input5,
    pub leds: (Output<'static, PB12>, Output<'static, PB13>, Output<'static, PB14>)
}

#[embassy_executor::task]
async fn run_iwdg(mut iwdg: IndependentWatchdog<'static, IWDG>) -> ! {
    let mut ticker = Ticker::every(Duration::from_millis(256));
    loop {
        iwdg.pet();
        ticker.next().await;
    }
}

async fn run_role<R: BoardRole>(p: embassy_stm32::Peripherals, low_priority_spawner: Spawner) {
    defmt::info!("Running as role {:?}", defmt::Debug2Format(&R::ROLE_ID));

    let mut adc = Adc::new(p.ADC1, &mut Delay);
    adc.set_sample_time(embassy_stm32::adc::SampleTime::Cycles239_5);

    let led_red = Output::new(p.PB12, Level::Low, Speed::Low);
    let led_white = Output::new(p.PB13, Level::Low, Speed::Low);
    let led_yellow = Output::new(p.PB14, Level::Low, Speed::Low);
    let leds = (led_red, led_white, led_yellow);

    let mut iwdg = IndependentWatchdog::new(p.IWDG, 512_000); // 512ms timeout
    iwdg.unleash();

    let input0 = match R::input0_mode() { // J7
        _ => Input0::Disabled,
    };

    let (boost_converter, input1) = match (R::boost_converter_voltage(), R::input1_mode()) { // J6
        (Some(v), InputMode::Disabled) => (
            Some((I2c::new(p.I2C2, p.PB10, p.PB11, Irqs, p.DMA1_CH4, p.DMA1_CH5, Hertz::khz(400), Default::default()), v)),
            Input1::Disabled
        ),
        (Some(_v), _) => unreachable!(),
        (None, InputMode::Uart(config)) => (None, Input1::Uart(Uart::new(p.USART3, p.PB11, p.PB10, Irqs, p.DMA1_CH2, p.DMA1_CH3, config).unwrap())),
        (None, InputMode::I2c(freq, config)) => (None, Input1::I2c(I2c::new(p.I2C2, p.PB10, p.PB11, Irqs, p.DMA1_CH4, p.DMA1_CH5, freq, config))),
        (None, _) => (None, Input1::Disabled),
    };

    let input2 = match R::input2_mode() { // J5
        InputMode::Uart(_) => todo!(),
        InputMode::Adc => todo!(),
        _ => Input2::Disabled,
    };

    let input3 = match R::input3_mode() { // J4
        InputMode::Uart(_) => todo!(),
        InputMode::I2c(freq, config) => Input3::I2c(I2c::new(p.I2C1, p.PB6, p.PB7, Irqs, p.DMA1_CH6, p.DMA1_CH7, freq, config)),
        InputMode::Gpio(pull) => Input3::Gpio(Input::new(p.PB6, pull), Input::new(p.PB7, pull)),
        _ => Input3::Disabled,
    };

    let input4 = match R::input4_mode() { // J12
        InputMode::Adc => todo!(),
        _ => Input4::Disabled,
    };

    let input5 = match R::input5_mode() { // J13
        InputMode::Adc => todo!(),
        _ => Input5::Disabled,
    };

    let io = BoardIo {
        input0,
        input1,
        input2,
        input3,
        input4,
        input5,
        leds,
    };

    let can_in = CAN_IN.init(PubSubChannel::new());
    let can_out = CAN_OUT.init(PubSubChannel::new());
    let output_state = OUTPUT_STATE.init(PubSubChannel::new());

    let mut can = embassy_stm32::can::Can::new(p.CAN, p.PA11, p.PA12, Irqs);
    R::configure_can(&mut can);

    // Start high priority executor
    interrupt::SPI2.set_priority(Priority::P6);
    let high_priority_spawner = EXECUTOR_HIGH.start(interrupt::SPI2);

    // Control output state based on received commands, with optional
    // failsafe behaviour if connection to FC is lost.
    high_priority_spawner.spawn(run_output_control_via_can(
        can_in.subscriber().unwrap(),
        output_state.publisher().unwrap(),
        R::ROLE_ID,
        R::output_failsafe_duration()
    )).unwrap();

    // Run output based on published output state
    high_priority_spawner.spawn(run_outputs(
        (Output::new(p.PC7, Level::Low, Speed::Low), Output::new(p.PC6, Level::Low, Speed::Low)),
        (Output::new(p.PC9, Level::Low, Speed::Low), Output::new(p.PC8, Level::Low, Speed::Low)),
        (Output::new(p.PB8, Level::Low, Speed::Low), Output::new(p.PB9, Level::Low, Speed::Low)),
        (Output::new(p.PA0, Level::Low, Speed::Low), Output::new(p.PA1, Level::Low, Speed::Low)),
        output_state.subscriber().unwrap(),
    )).unwrap();

    // Run CAN bus, publishing received messages on can_in and transmitting messages
    // published on can_out.
    can::spawn(can, low_priority_spawner, can_in.publisher().unwrap(), can_out.subscriber().unwrap()).await;

    // Run the independent watchdog
    low_priority_spawner.spawn(run_iwdg(iwdg)).unwrap();

    // Every IO board occasionally reports its temperature, drive voltage and current
    low_priority_spawner.spawn(run_power_report(
        can_out.publisher().unwrap(),
        adc,
        p.PA7,
        p.PA6,
        p.PA5,
        p.PB1,
        p.PA4,
        R::ROLE_ID,
        R::drive_voltage()
    )).unwrap();

    // Run a listener that enables all outputs after a certain
    // flight mode if requested by the rol
    if let Some(fm) = R::outputs_on_after_flightmode() {
        high_priority_spawner.spawn(run_outputs_on_after_flightmode(
            can_in.subscriber().unwrap(),
            output_state.publisher().unwrap(),
            fm
        )).unwrap();
    }

    // Run the boost converter if requested by the role.
    if let Some((i2c, target_voltage)) = boost_converter {
        let enable_output = Output::new(p.PB0, Level::Low, Speed::Low);
        low_priority_spawner.spawn(run_boost_converter(i2c, target_voltage, enable_output)).unwrap();
    }

    // Allow role to spawn its own tasks
    R::spawn(io, high_priority_spawner, low_priority_spawner, can_in, can_out, output_state);
}

#[embassy_executor::main]
async fn main(spawner: Spawner) {
    let mut config = Config::default();
    config.rcc.hse = Some(Hertz::mhz(8));
    config.rcc.sys_ck = Some(Hertz::mhz(72));
    config.rcc.hclk = Some(Hertz::mhz(72));
    config.rcc.pclk1 = Some(Hertz::mhz(36));
    config.rcc.pclk2 = Some(Hertz::mhz(72));
    config.rcc.adcclk = Some(Hertz::mhz(14));
    let mut p = embassy_stm32::init(config);

    // We need to borrow the peripherals for the pins so we can later pass the
    // entire Peripherals struct to the role function.
    let dip_switch_setting = {
        let role_sw1 = Input::new(&mut p.PC4, embassy_stm32::gpio::Pull::Down);
        let role_sw2 = Input::new(&mut p.PC5, embassy_stm32::gpio::Pull::Down);
        let role_sw3 = Input::new(&mut p.PB15, embassy_stm32::gpio::Pull::Down);
        let role_sw4 = Input::new(&mut p.PA8, embassy_stm32::gpio::Pull::Down);
        let role_sw5 = Input::new(&mut p.PA9, embassy_stm32::gpio::Pull::Down);
        ((role_sw1.is_high() as u8) << 4) |
            ((role_sw2.is_high() as u8) << 3) |
            ((role_sw3.is_high() as u8) << 2) |
            ((role_sw4.is_high() as u8) << 1) |
            (role_sw5.is_high() as u8)
    };

    match IoBoardRole::try_from(dip_switch_setting) {
        Ok(IoBoardRole::Acs) => run_role::<Acs>(p, spawner).await,
        Ok(IoBoardRole::Recovery) => run_role::<Recovery>(p, spawner).await,
        Ok(IoBoardRole::Payload) => run_role::<Payload>(p, spawner).await,
        Err(id) => {
            loop {
                defmt::error!("Unknown role: {:05b}", id);
                Timer::after(Duration::from_millis(100)).await;
            }
        }
    }
}

#[interrupt]
unsafe fn SPI2() {
    EXECUTOR_HIGH.on_interrupt()
}

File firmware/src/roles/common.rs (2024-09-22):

use embassy_stm32::gpio::{Input, Output};
use embassy_stm32::adc::Adc;
use embassy_stm32::i2c::I2c;
use embassy_stm32::peripherals::*;
use embassy_time::{Delay, Ticker};
use embassy_time::{with_timeout, Duration};
use embedded_hal::digital::OutputPin;

use shared_types::*;

use crate::{CanInSubscriper, DriveVoltage, OutputStatePublisher, OutputStateSubscriber};

async fn receive_output_message(
    subscriber: &mut crate::CanInSubscriper,
    role: IoBoardRole,
    command_id: u8
) -> IoBoardOutputMessage {
    let expected_sid = CanBusMessageId::IoBoardCommand(role, command_id).into();

    loop {
        match subscriber.next_message_pure().await {
            (sid, data) if sid == expected_sid => {
                if let Ok(Some(msg)) = IoBoardOutputMessage::parse(data) {
                    return msg;
                }
            },
            _ => {}
        }
    }
}

async fn receive_telemetry_message(
    subscriber: &mut crate::CanInSubscriper,
) -> TelemetryToPayloadMessage {
    let expected_sid = CanBusMessageId::TelemetryBroadcast(0).into();

    loop {
        match subscriber.next_message_pure().await {
            (sid, data) if sid == expected_sid => {
                if let Ok(Some(msg)) = TelemetryToPayloadMessage::parse(data) {
                    return msg;
                }
            }
            _ => {}
        }
    }
}

#[embassy_executor::task]
pub async fn run_outputs(
    mut output0: (Output<'static, PC7>, Output<'static, PC6>),
    mut output1: (Output<'static, PC9>, Output<'static, PC8>),
    mut output2: (Output<'static, PB8>, Output<'static, PB9>),
    mut output3: (Output<'static, PA0>, Output<'static, PA1>),
    mut subscriber: OutputStateSubscriber,
) -> ! {
    loop {
        let (outputs, _failsafe) = subscriber.next_message_pure().await;
        output0.0.set_level(outputs[0].into());
        output0.1.set_level(outputs[1].into());
        output1.0.set_level(outputs[2].into());
        output1.1.set_level(outputs[3].into());
        output2.0.set_level(outputs[4].into());
        output2.1.set_level(outputs[5].into());
        output3.0.set_level(outputs[6].into());
        output3.1.set_level(outputs[7].into());
    }
}

#[embassy_executor::task]
pub async fn run_output_control_via_can(
    mut can_subscriber: CanInSubscriper,
    output_publisher: OutputStatePublisher,
    role: IoBoardRole,
    timeout: Option<Duration>,
) -> ! {
    loop {
        let (outputs, failsafe) = if let Some(timeout) = timeout {
            match with_timeout(timeout, receive_output_message(&mut can_subscriber, role, 0)).await {
                Ok(msg) => (msg.outputs, false),
                Err(_) => ([false; 8], true)
            }
        } else {
            (receive_output_message(&mut can_subscriber, role, 0).await.outputs, false)
        };

        output_publisher.publish_immediate((outputs, failsafe));
    }
}

async fn read_i2c_amp_value<I2C: embedded_hal_async::i2c::I2c>(
    i2c: &mut I2C,
    i2c_address: u8
) -> Result<(u16, bool), I2C::Error> {
    // https://www.ti.com/lit/ds/symlink/adc101c027.pdf
    let mut buffer: [u8; 2] = [0x00, 0x00];
    i2c.read(i2c_address, &mut buffer).await?;

    let conversion_register = u16::from_be_bytes(buffer);
    let alert_flag = (conversion_register >> 15) > 0;
    let conversion_result = (conversion_register >> 2) & 0x3ff;

    Ok((conversion_result, alert_flag))
}

#[embassy_executor::task]
pub async fn run_i2c_sensors(
    mut input1_i2c: Option<I2c<'static, I2C2, DMA1_CH4, DMA1_CH5>>,
    mut input3_i2c: Option<I2c<'static, I2C1, DMA1_CH6, DMA1_CH7>>,
    mut input3_gpio: Option<(Input<'static, PB6>, Input<'static, PB7>)>,
    publisher: crate::CanOutPublisher,
    role: IoBoardRole,
    interval: Duration,
) -> ! {
    // ADC101C027 addresses in order: ADR floating, GND, VCC
    const AMPLIFIER_ADDRESSES: [u8; 3] = [0b1010000, 0b1010001, 0b1010010];

    let mut ticker = Ticker::every(interval);
    loop {
        // If we use both busses for sensors, we assume that each I2C bus has
        // two sensors, allowing us to fill all four slots of a single sensor
        // message. If we use just one, we can do up to 3 sensors per bus.
        let i2c_sensors = match (input1_i2c.as_mut(), input3_i2c.as_mut(), input3_gpio.as_mut()) {
            (Some(i2c2), Some(i2c1), _) => [
                read_i2c_amp_value(i2c2, AMPLIFIER_ADDRESSES[0]).await.ok(),
                read_i2c_amp_value(i2c2, AMPLIFIER_ADDRESSES[1]).await.ok(),
                read_i2c_amp_value(i2c1, AMPLIFIER_ADDRESSES[0]).await.ok(),
                read_i2c_amp_value(i2c1, AMPLIFIER_ADDRESSES[1]).await.ok(),
            ],
            (Some(i2c2), None, pins) => [
                read_i2c_amp_value(i2c2, AMPLIFIER_ADDRESSES[0]).await.ok(),
                read_i2c_amp_value(i2c2, AMPLIFIER_ADDRESSES[1]).await.ok(),
                read_i2c_amp_value(i2c2, AMPLIFIER_ADDRESSES[2]).await.ok(),
                pins.map(|(p0, p1)| (((p0.is_high() as u16) << 1 | (p1.is_high() as u16), false))),
            ],
            (None, Some(i2c1), _) => [
                read_i2c_amp_value(i2c1, AMPLIFIER_ADDRESSES[0]).await.ok(),
                read_i2c_amp_value(i2c1, AMPLIFIER_ADDRESSES[1]).await.ok(),
                read_i2c_amp_value(i2c1, AMPLIFIER_ADDRESSES[2]).await.ok(),
                None,
            ],
            (None, None, _) => unreachable!(),
        };

        let msg = IoBoardSensorMessage { i2c_sensors };
        let (id, msg) = msg.to_frame(CanBusMessageId::IoBoardInput(role, 0));
        publisher.publish_immediate((id, msg));

        ticker.next().await;
    }
}

fn to_millivolts(vref_sample: u16, sample: u16) -> u16 {
    const VREFINT_MV: u32 = 1200; // mV
    (u32::from(sample) * VREFINT_MV / u32::from(vref_sample)) as u16
}
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

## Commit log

2023-12-28 basic microcontroller peripherals
    [frodo_io_module.kicad_sch]
2024-01-06 USART Pin Configuration
    [frodo_io_module.kicad_sch]
2024-01-09 voltage regulator addition
    [frodo_io_module.kicad_sch]
2024-01-29 dip switch addition
    [frodo_io_module.kicad_sch]
2024-01-29 mosfet addition
    [frodo_io_module.kicad_sch]
2024-02-27 label addition and switch changes
    [frodo_io_module.kicad_sch]
2024-03-07 dip s
    [dip_switch.kicad_sch]
2024-03-08 cleanup/commenting for better readability, minor corrections
    [digital_output.kicad_sch, dip_switch.kicad_sch, frodo_io_module.kicad_sch]
2024-03-16 Add flash, CAN transceiver, 5V regulators, power filtering; minor corrections
    [frodo_io_module.kicad_sch]
2024-03-17 Add boost converter schematics
    [frodo_io_module.kicad_sch]
2024-03-17 Add test points
    [frodo_io_module.kicad_sch]
2024-03-17 Add I2C pull-up resistors and digital output flyback diodes
    [digital_output.kicad_sch, frodo_io_module.kicad_sch]
2024-03-17 Add voltage sensing, Correct resistor value
    [frodo_io_module.kicad_sch]
2024-03-29 footprints assigned
    [frodo_io_module.kicad_sch]
2024-03-29 more footprints assigned
    [frodo_io_module.kicad_sch]
2024-03-30 Finish footprint assignment
    [digital_output.kicad_sch, frodo_io_module.kicad_sch]
2024-06-03 updates to the schematics, rough component placement in the PCB layout
    [digital_output.kicad_sch, frodo_io_module.kicad_pcb, frodo_io_module.kicad_sch]
2024-06-03 trace routing of boost converter section
    [frodo_io_module.kicad_pcb, frodo_io_module.kicad_sch]
2024-06-08 Resolved conflicts
    [digital_output.kicad_sch]
2024-06-19 routing traces
    [digital_output.kicad_sch, frodo_io_module.kicad_pcb, frodo_io_module.kicad_sch]
2024-06-21 recovery of schematics while keeping routed traces
    [digital_output.kicad_sch, frodo_io_module.kicad_sch]
2024-06-24 trace routing in component subgroups
    [frodo_io_module.kicad_pcb]
2024-06-24 add 3d models for Molex connectors and power inductor
    [430450400.step, 430450600.stp, PSM1365 Series SMD Molding inductor.STEP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]
2024-07-01 routing of power levels
    [frodo_io_module.kicad_pcb]
2024-07-01 add logos, name and revision text
    [frodo_io_module.kicad_pcb]
2024-07-01 route traces to JST-GH connectors and ICs, fix problem with swapped CAN Bus lines
    [frodo_io_module.kicad_pcb, frodo_io_module.kicad_sch]
2024-07-02 finish trace routing
    [frodo_io_module.kicad_pcb, frodo_io_module.kicad_sch]
2024-07-04 placement of default silkscreen symbols
    [frodo_io_module.kicad_pcb]
2024-07-04 add descriptors on silkscreen, add part numbers
    [digital_output.kicad_sch, frodo_io_module.kicad_pcb, frodo_io_module.kicad_sch]
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2024-09-22 Reuse single vref sample, invert current calculation
    [common.rs]
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2025-02-25 removed boost converter
    [digital_output.kicad_sch, frodo_io_module.kicad_sch]
2025-02-25 added vehicle bus
    [frodo_io_module.kicad_sch]
2025-04-08 minor changes
    [digital_output.kicad_sch, frodo_io_module.kicad_sch]
2025-04-16 updated scematic to new requirements
    [digital_output.kicad_sch, frodo_io_module.kicad_pcb, frodo_io_module.kicad_sch]
2025-04-18 some more changes to the io board
    [430450800.stp, digital_output.kicad_sch, frodo_io_module.kicad_pcb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]
2025-04-19 pin assignments
    [frodo_io_module.kicad_sch, pin assignment.xlsx]
2025-04-27 Organize Components into groups.
    [frodo_io_module.kicad_pcb]
2025-04-28 some more pin assignments
    [frodo_io_module.kicad_pcb, frodo_io_module.kicad_sch, pin assignment.xlsx]
2025-04-29 finished pin assignment, some changes to scematic
    [frodo_io_module.kicad_sch, pin assignment.xlsx]
2025-05-06 work on usb connector routing
    [frodo_io_module.kicad_pcb]
2025-05-07 fixed usb and some other issues
    [frodo_io_module.kicad_sch, pin assignment.xlsx]
2025-05-07 fixed usb, added footprints
    [digital_output.kicad_sch, frodo_io_module.kicad_pcb, frodo_io_module.kicad_sch]
2025-05-07 some more changes
    [digital_output.kicad_sch, frodo_io_module.kicad_pcb, frodo_io_module.kicad_sch]
2025-05-21 rough placement of the components
    [frodo_io_module.kicad_pcb, frodo_io_module.kicad_sch]
2025-05-26 basic routing
    [frodo_io_module.kicad_pcb]
2025-06-02 more routing
    [frodo_io_module.kicad_pcb, frodo_io_module.kicad_sch]
2025-06-02 remove second 3.3V reg and i2c pull up jumpers
    [frodo_io_module.kicad_pcb, frodo_io_module.kicad_sch]
2025-06-10 power routing
    [frodo_io_module.kicad_pcb]
2025-06-15 finish routing
    [frodo_io_module.kicad_pcb, frodo_io_module.kicad_sch]
2025-06-23 small routing improvements
    [frodo_io_module.kicad_pcb]
2025-07-03 added part numbers for all parts
    [frodo_io_module.kicad_sch]
2025-07-07 improve silkscreen
    [frodo_io_module.kicad_pcb]
2025-07-07 Fix ouput silkscreen number, clearance violation, start skew tuning (CAN)
    [frodo_io_module.kicad_pcb, frodo_io_module.kicad_sch]
2025-07-10 Revisit can trace tuning
    [frodo_io_module.kicad_pcb]
2026-02-16 started new design iteration, some scematic fixes (servo pwm&5v option, tsv issue)
    [frodo_io_module.kicad_pcb, frodo_io_module.kicad_sch, pin assignment.xlsx]
2026-02-16 added comment for mosfet todo
    [digital_output.kicad_sch, frodo_io_module.kicad_pcb, frodo_io_module.kicad_sch]
2026-02-23 fixed transistor rotation issue, filter vs farrite bead, 5V supply for servos, and others in scematic
    [digital_output.kicad_sch, frodo_io_module.kicad_pcb, frodo_io_module.kicad_sch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]
2026-05-20 started routing
    [digital_output.kicad_sch, frodo_io_module.kicad_pcb, frodo_io_module.kicad_sch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]
2026-05-20 added sub scematics
    [current_sensing.kicad_sch, pin assignment.xlsx]
2026-06-11 finished routing
    [digital_output.kicad_sch, frodo_io_module.kicad_pcb, frodo_io_module.kicad_sch]
2026-06-11 started silkscrean
    [current_sensing.kicad_sch, digital_output.kicad_sch, frodo_io_module.kicad_pcb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]
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2026-06-17 most current state, adapt thermal cutouts in layers
    [frodo_io_module.kicad_sch]
2026-06-23 high current inputs: change pmos pullup and led resistors
    Apparently Kicad also saved files in a new format.
    I was using Kicad version 10.0
    [current_sensing.kicad_sch, digital_output.kicad_sch, frodo_io_module.kicad_sch]
2026-06-26 silkscreen improvements, change mosfets, fix diode footprint
    [current_sensing.kicad_sch, digital_output.kicad_sch, frodo_io_module.kicad_pcb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]
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2026-06-27 some last adaptaions while ordering
    [bom.csv, current_sensing.kicad_sch, digital_output.kicad_sch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]
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

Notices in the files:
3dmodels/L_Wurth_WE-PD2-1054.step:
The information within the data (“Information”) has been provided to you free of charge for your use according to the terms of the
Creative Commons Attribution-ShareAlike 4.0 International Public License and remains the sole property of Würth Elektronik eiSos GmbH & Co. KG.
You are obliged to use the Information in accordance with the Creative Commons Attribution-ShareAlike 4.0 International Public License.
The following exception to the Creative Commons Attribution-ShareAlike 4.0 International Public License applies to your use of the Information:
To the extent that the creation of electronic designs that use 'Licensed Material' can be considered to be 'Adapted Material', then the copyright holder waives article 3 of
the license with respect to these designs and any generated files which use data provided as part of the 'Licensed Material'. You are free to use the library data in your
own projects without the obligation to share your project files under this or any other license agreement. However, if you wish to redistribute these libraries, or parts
